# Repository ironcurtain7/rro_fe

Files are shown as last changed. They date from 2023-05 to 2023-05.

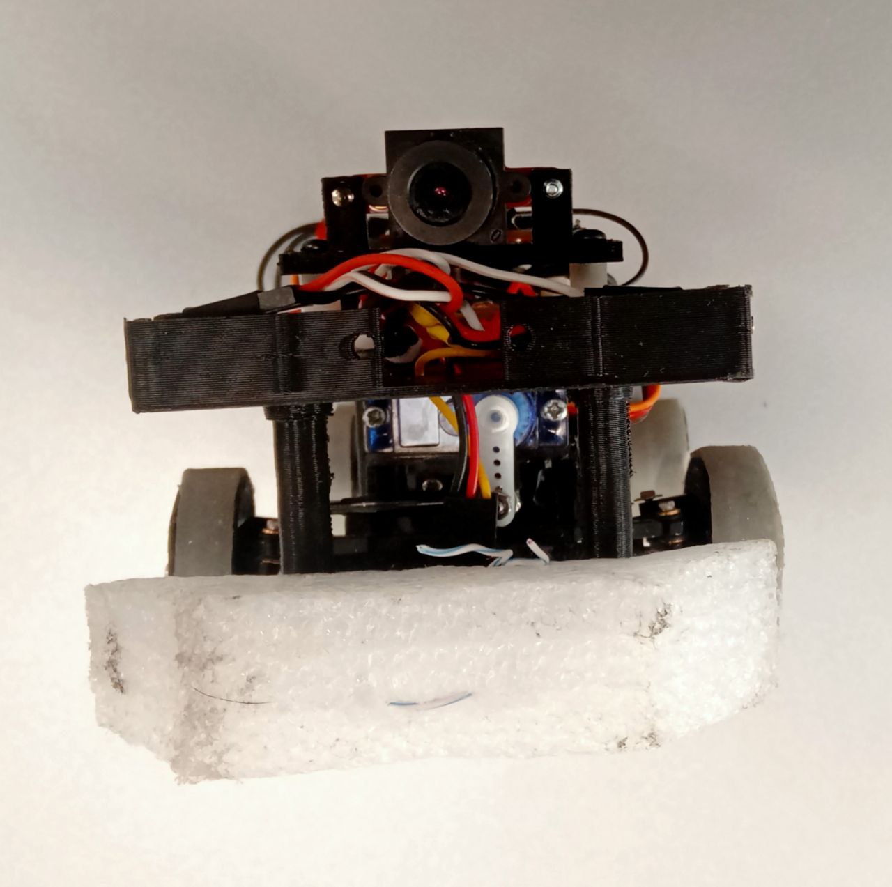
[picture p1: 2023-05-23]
v-photos/5.jpg

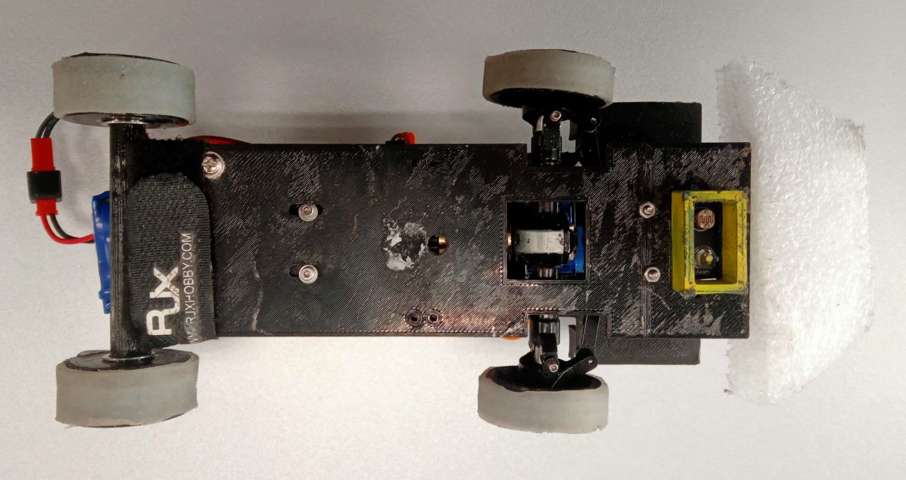
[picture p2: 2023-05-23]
v-photos/3.jpg

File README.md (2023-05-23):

Команда Роботикс (Robotx). Описание робота для соревновний FutureEngineers 2023.

Робот был сделан на основе самостоятельно разработанного и напечатанного на 3D-принтере шасси. 3D модели для печати находятся в папке models. 
Вариант самостоятельной разработки шасси был выбран по двум причинам: 
- возможность сделать шасси нужной конфигурации для оптимального расположения электронных и механических компонентов робота 
- уменьшения массы робота и улучшенния маневренности по сравнению с готовыми радиоуправляемыми шасси

Система перемещения робота:

Шасси робота состоит из следующих частей: 
непосредственно рамы шасси (car_frame.stl), 
креплений мотора, рулевого сервопривода и камеры (motor_mount.stl, servo_mount.stl,camera_mount.stl),
дисков колес (rim.stl) и вылитых из силикона шин (формы для отливки: wheels1.stl, wheels2.stl)

Шины решили делать из силикона, т.к. можно сделать любую необходимую форму шины и выбрать мягкость шины для максимального сцепления с поверхностью.

А так же используется передний мост от радиоуправляемой модели автомобиля размера 1/24 (Фото: other/axle.jpg) для того, чтобы сделать робота переднеприводным для улучшения маневренности. В мосту стоит 
червячный редуктор для уменьшения передаваемых на колеса оборотов от двигателя.

Основной двигатель: Readytosky rs2205, бесколлекторный, размера 2205, 2200 оборотов. Управляется через регулятор двигателя (модель LittleBee 30A-S) ШИМ-сигналом с ESP32. Возможен передний и задний ход.
Обороты двигателя выбраны исходя из передаточного числа редуктора в мосту 1 к 15.
Двигатель и привод переднего моста соединены латунной муфтой (Фото: other/muff.jpg).

Сервопривод поворота колес: Tower Pro MG90S, 9 грамм

Так как шасси было специально разработано для вышеуказанных компонентов, то все части шасси собираются вместе с помощью винтов и гаек M3/M4 без какой-либо дополнительной подготовки. 

Система питания:

В роботе используется одна батарея LiPo 2s (7.4V) 1100mAh. Подключена через выключатель. От нее через регулятор двигателя питается собственно двигатель. А так же через DC-DC 
преобразователь на 5В питается вся остальная электроника. Для сглаживания падения напряжения от работы двигателя в схеме предусмотрен конденсатор 16v, 2200мкФ, подключенный 
параллельно батарее.

Контроллеры и сенсоры:

В роботе используется два микроконтроллера: 
ESP32 - основной контроллер. Используется для выполнения всей логики программы, управления основным и рулевым приводом, обработка данных с датчиков.
OpenMV H7 - контроллер анализа изображения с камеры. Анализирует изображение, находит необходимые объекты и передает данные по найденным объектам в основной контроллер.
Передача происходит по Serial порту. Данные контроллеры были выбраны по причине малых размеров, низкого энергопотребления, большого количества портов для сенсоров
 и достаточной для данной задачи производительности.

Используемые сенсоры:

- лазерный дальномер VL53L0X - используется для определения расстояния до стен полигона. Установлены по одному справа и слева в передней части робота.
- фототранзистор со светодиодной подствекой - используется для определения цвета линий на поверхности полигона путем анализа яркости отражаемого света. Т.е. яркость отраженного света
от линий белого, синего и оранжевого цвета различается и на этой основе определяется цвет линий.
- кнопка старта робота

Схема подключения системы питания к контроллерам, двигателям, а так же сенсоров к контроллеру находится в папке schemes (scheme.jpg).
Для уменьшения количества проводов между контроллерами и датчиками была спроектирована в программе SprintLayot и вытравлена на текстолите плата, на которую уже паялись разъемы для контроллеров и подключались датчики.
Ее схема так же находится в папке schemes (Плата FE.lay6).

Робот включается с помощью выключателя на кабеле к батарее. Запускаются оба контроллера. После этого ESP32 инициализирует регулятор/основной двигатель (издается звуковой сигнал) и ждет нажатия на кнопку старта.

Логика работы программы:

Квалификационный заезд (робот устанавливается на поле строго вдоль бортов, основная программа начинает работать после нажатия кнопки старта):

1. Робот определяет свою позицию относительно стенок полигона. Т.е. определяет расстояние до стены справа и слева с помощью дальномеров.
2. Двигается вперед строго прямо до нахождения синей/оранжевой полосы с помощью датчика яркости света
3. Если найдена синяя/оранжевая полоса, то в зависимости от ранее определенной позиции, робот едет с поворотом колес налево/направо на нужный угол необходимое количество 
времени таким образом, чтобы подъехать к перпендикулярной стене на расстояние примерно 20см и встать вдоль нее. Угол и время проезда подбирается опытным путем.
4. Затем запускается блок программы езды вдоль внешней стены полигона с помощью дальномеров и PID-регулятора. Робот едет на расстоянии 20см от внешней стены. Т.е. если первый поворот был налево 
и внешняя стенка справа, то едем по правому дальномеру. И наоборот.
5. Во время езды вдоль стены анализируем показания датчика яркости и определяем наезд на синюю/оранжевую линию.
6. Если наехали на синюю/оранжевую линию, то робот поворачивает колеса на нужный угол налево/направо и проезжает неободимое количество времени для того, чтобы подъехать к 
перпендикулярной стене на расстояние 20см и встать вдоль нее. Угол и время проезда подбирается опытным путем.
7. Затем алгоритм повторяется с п.4 до тех пор пока количество поворотов не достигнет 12.
8. После проезда двенадцатого поворота проезжаем заранее подобранное время с заранее подобранным углом поворота колес и останавливаемся.

Финальный заезд (робот устанавливается на поле строго вдоль бортов, основная программа начинает работать после нажатия кнопки старта):
1. Робот определяет свою позицию относительно стенок полигона. Т.е. определяет расстояние до стены справа и слева с помощью дальномеров.
2. Двигается вперед строго прямо до нахождения синей/оранжевой полосы с помощью датчика яркости света.
3. Если найдена синяя/оранжевая полоса, то в зависимости от ранее определенной позиции, робот едет с поворотом колес налево/направо на нужный угол необходимое количество 
времени таким образом, чтобы подъехать к перпендикулярной стене на расстояние примерно 20см и встать вдоль нее. Угол и время проезда подбирается опытным путем.
4. Затем запускается блок программы езды вдоль внешней стены полигона с помощью дальномеров и PID-регулятора. Робот едет на расстоянии 20см от внешней стены. Т.е. если первый поворот был налево 
и внешняя стенка справа, то едем по правому дальномеру. И наоборот.
5. Во время езды вдоль стены анализируем показания с контроллера OpenMV H7. Если контроллер OpenMV находит препятствие, то передает данные о цвете и координатах препятствия на контроллер ESP32. 
ESP32 направляет робота в течение 1 секунды на препятсвие (постоянно получая данные с OpenMV о координатах препятсвия) для того, чтобы выровнять робота относительно препятствия. Т.е. препятсвие через одну секунду будет находиться строго перед роботом. 
Далее робот делает маневр объезда препятсвия в зависимости от цвета слева или справа. Объезд (углы поворота колес и время проезда) настраивается опытным путем. После объезда робот снова начинает ехать вдоль внешней стены.
6. Одновременно с получением данных с OpenMV, контроллер ESP32 анализирует показания датчика яркости и определяет наезд на синюю/оранжевую линию.
7. Если наехали на синюю/оранжевую линию, то робот поворачивает колеса на нужный угол налево/направо и проезжает неободимое количество времени для того, чтобы подъехать к 
перпендикулярной стене на расстояние 20см и встать вдоль нее. Угол и время проезда подбирается опытным путем.
8. Затем алгоритм повторяется с п.4 до тех пор пока количество поворотов не достигнет 12.
9. После проезда двенадцатого поворота проезжаем заранее подобранное время с заранее подобранным углом поворота колес и останавливаемся.

Программа для ESP32 написана на языке C++, для OpenMV - на языке python. Исходный код находится в папке src.

qual.cpp - программа для квалификационного заезда на ESP32

final.cpp - программа для финального заезда на ESP32

main.py - программа для контроллера OpenMV H7

Программы для ESP32 используют стандартные библиотеки из фреймворка PlatformIO, компилируются и загружаются в контроллер в среде Microsoft Visual Studio Code.
Программа для OpenMV H7 загружается в контроллер с помощью стандартной среды разработки от контроллеров OpenMV. (Скачать можно по ссылке https://openmv.io/pages/download)

Программы для квалификационного и финального заездов во многом схожи и состоят из таких блоков:
1. Блок добавления библиотек, определения переменных и создание объектов для управления сервоприводом, основным двигателем и дальномерами.
2. Функция SetID(). Инициализация лазерных дальномеров. Указание их режима и параметров работы.
3. Функция start(). Определение положения робота относительно стенок полигона, проезд до первого поворота, определение направления поворота и непосредственно выполнение поворота.
4. Функция setup(). Настройка параметров serial порта для передачи данных с контроллера OpenMV. Ожидание нажатия кнопки старта и запуск функции start() после нажатия кнопки.
5. Функция loop(). Основной цикл программы. В ней реализована вся логика программы описанная выше.

В программе для контроллера OpenMV H7 следующие блоки:
1. Импорт библиотек и определение переменных
2. Определение порогов цветов в цветовой модели LAB для определения объектов красного и зеленого цветов.
3. Настройка serial порта и режима работы камеры
4. Блок определения красных объектов в необходимой области видимости (ROI) и передача цвета и х-координаты в контроллер ESP32 по serial порту.
5. Блок определения зеленых объектов в необходимой области видимости (ROI) и передача цвета и х-координаты в контроллер ESP32 по serial порту.

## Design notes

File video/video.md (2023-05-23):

Квалификационный заезд: https://youtu.be/G_IELsaBGgg

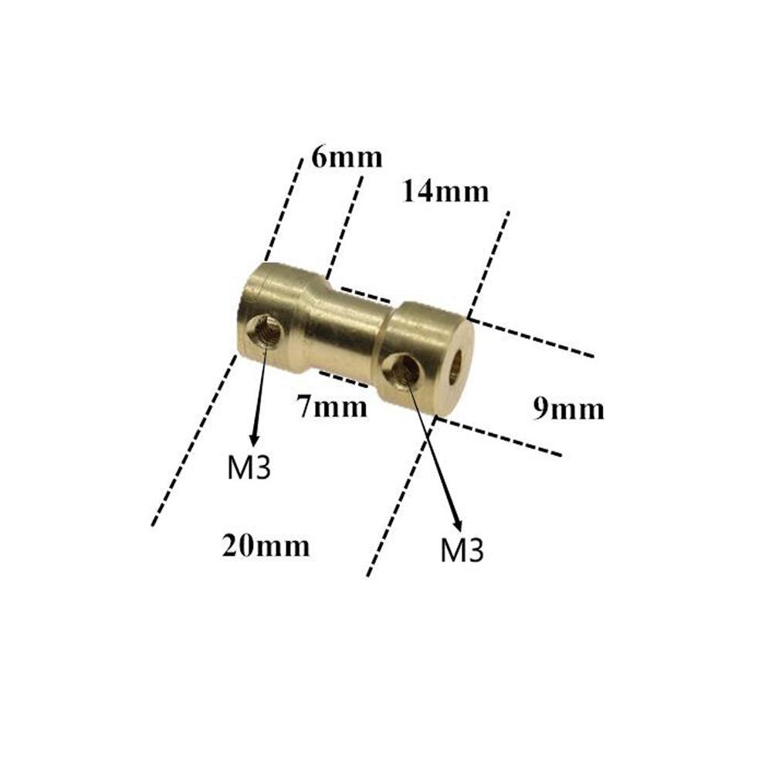
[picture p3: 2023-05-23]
other/muff.jpg

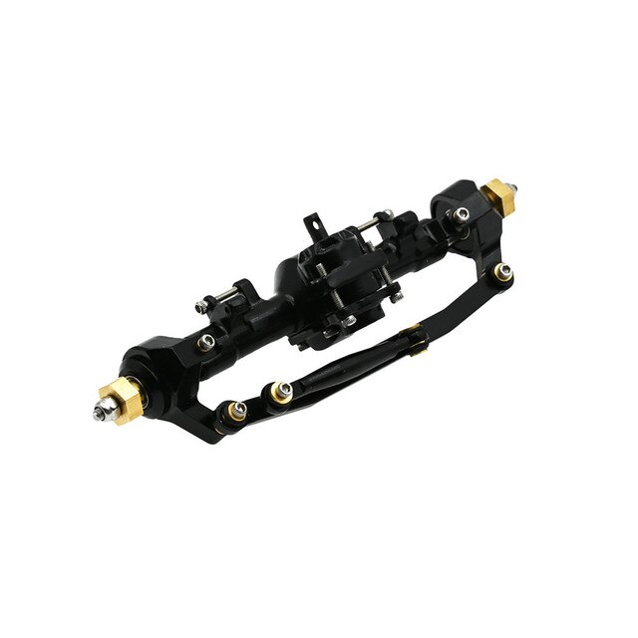
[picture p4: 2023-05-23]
other/axle.jpg

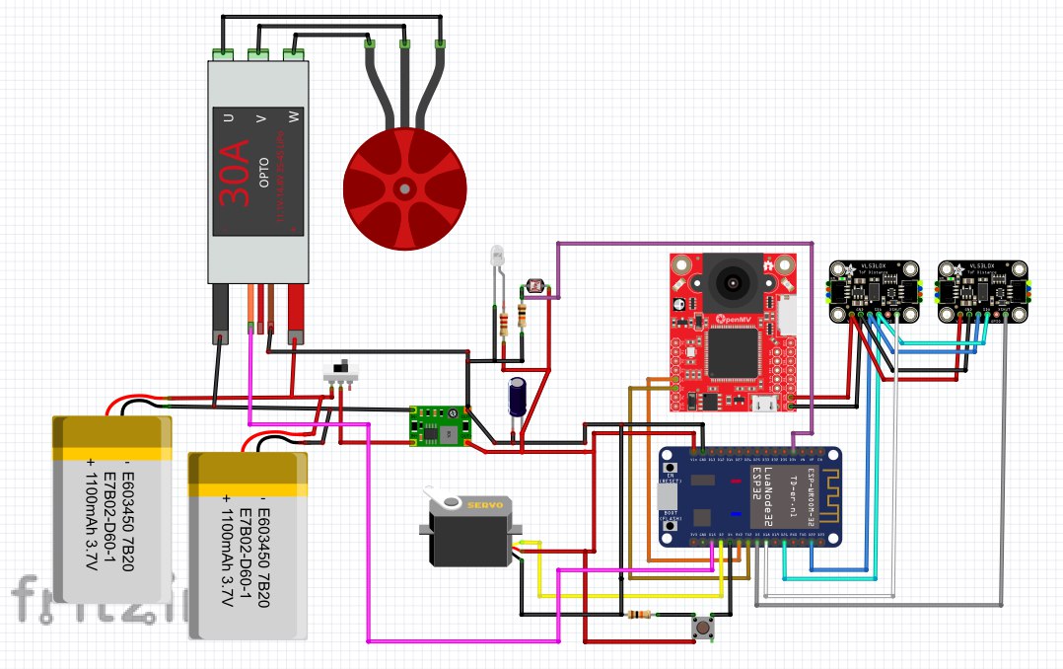
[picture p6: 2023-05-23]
schemes/scheme.jpg

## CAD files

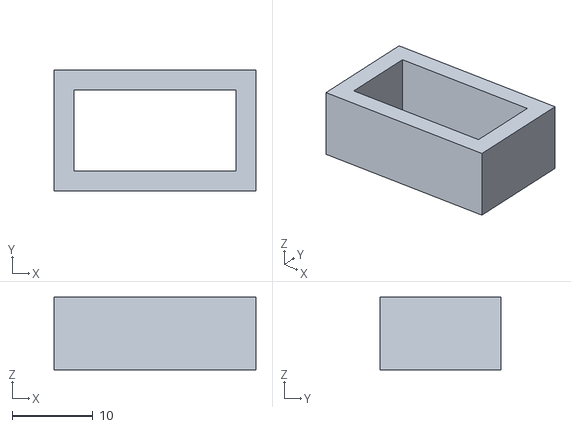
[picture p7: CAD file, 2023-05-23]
models/servo_mount.stl
25.0 x 15.0 x 9.00

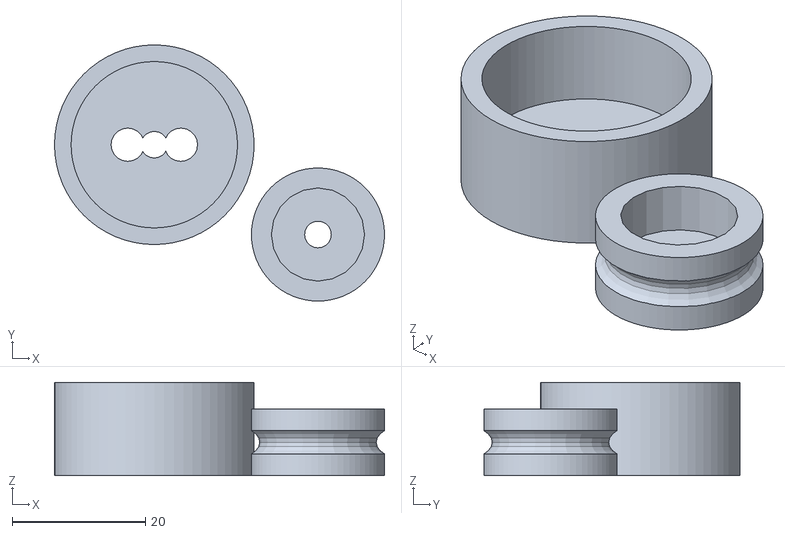
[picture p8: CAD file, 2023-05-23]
models/wheels2.stl
49.6 x 38.5 x 14.0

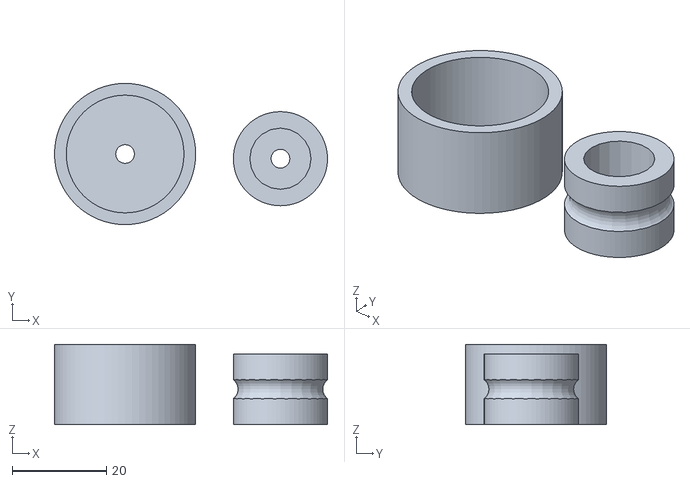
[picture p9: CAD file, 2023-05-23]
models/wheels1.stl
58.0 x 30.0 x 17.0

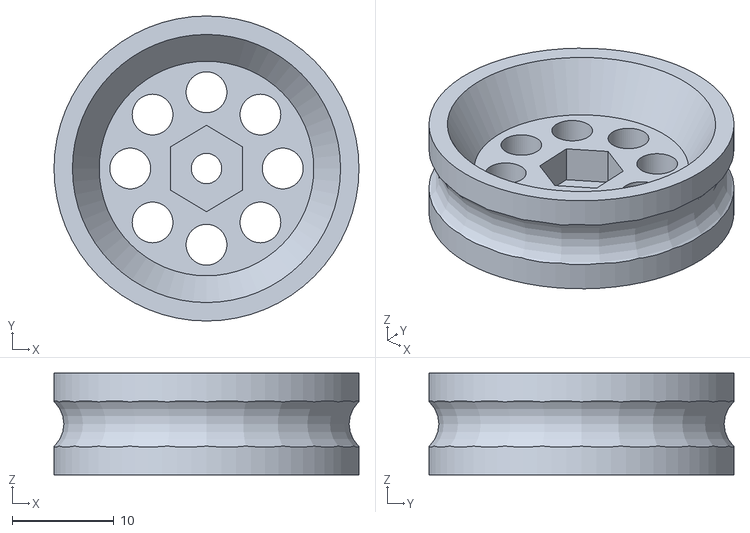
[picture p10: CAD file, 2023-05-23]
models/rim.stl
30.0 x 30.0 x 10.0

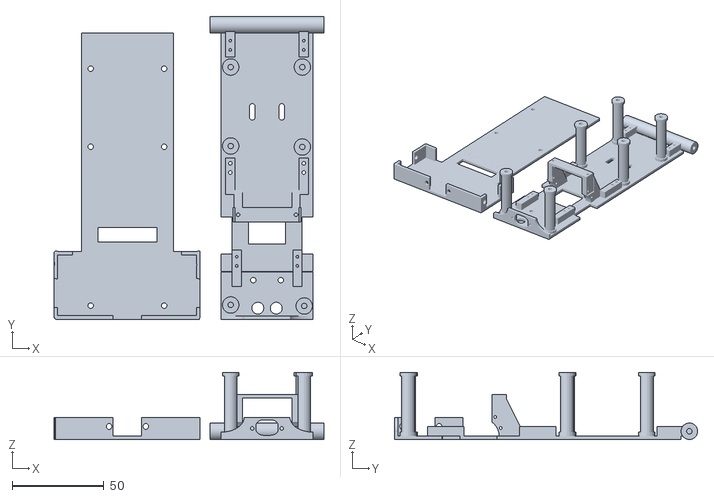
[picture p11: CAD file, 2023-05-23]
models/car_frame.stl
147.0 x 165.1 x 36.5

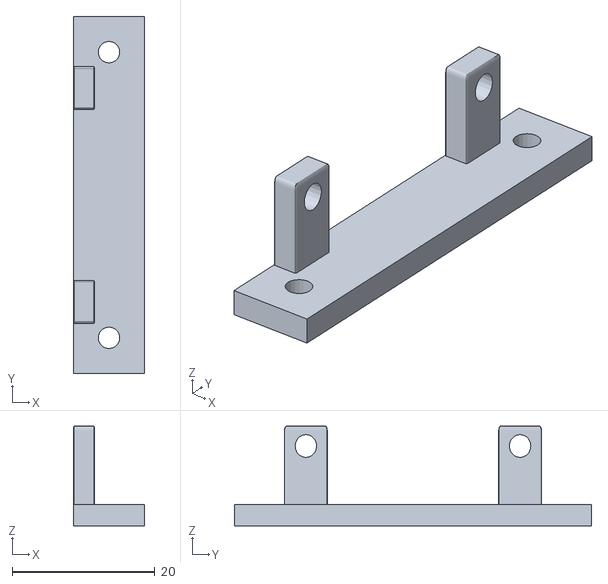
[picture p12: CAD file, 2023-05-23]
models/camera_mount.stl
10.0 x 50.0 x 14.0

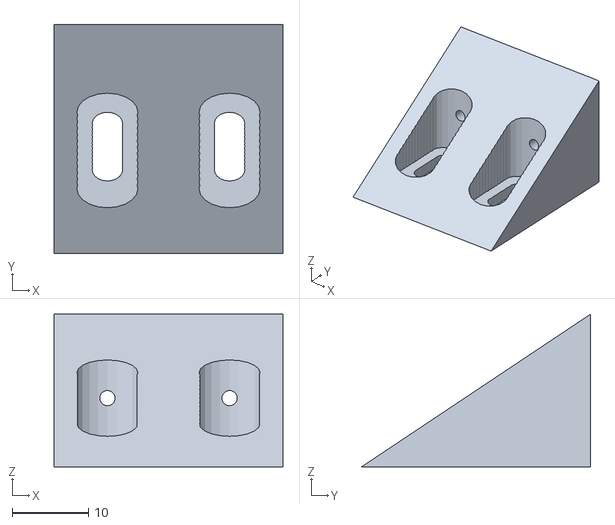
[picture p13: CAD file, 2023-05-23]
models/motor_mount.stl
30.0 x 30.0 x 20.0

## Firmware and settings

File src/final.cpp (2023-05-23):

// Добавление всех необходимых библиотек //
#include <Arduino.h>
#include "Adafruit_VL53L0X.h"
#include <Servo.h>

// Создание переменных //
#define RXD2 16
#define TXD2 17

int P;
int I;
int D;
int white = 3500;
int blue = 3270;
int timing = 700;
int lastError = 0, j, startflag, error;

int cx, millisold = 0;
int speed = 98;

int oldmil;
char color;
float Kp=0.1, Ki=0, Kd=1;
int16_t Fread, Lread, Rread, LigR, ButR = 0, count = 0;
const char* ssid = "DIR-615-effb";
const char* password = "18050523";
constexpr size_t size = 1000;
double numbers[size] {0}; 
int flag = 0, u, turn, porog;
int distance, sum  = 0, i = 0, sum1 = 0, Min = 9999;
int timMilis;
int timOLD;

int tim1 = 1000, tim2 = 1000, tim3 = 1000, ang1 = 65, ang2 = 65, ang3 = 65;







String Kp_text = String(Kp, 5);
String Ki_text = String(Ki, 5);
String Kd_text = String(Kd, 5);
String white_text = String(white);
String blue_text = String(blue);
String speed_text = String(speed);
String timing_text = String(timing);

String tim1_text = String(tim1);
String tim2_text = String(tim2);
String tim3_text = String(tim3);

String ang1_text = String(ang1);
String ang2_text = String(ang2);
String ang3_text = String(ang3);





// Adafruit_VL53L0X lox = Adafruit_VL53L0X();
Adafruit_VL53L0X lox1 = Adafruit_VL53L0X();
Adafruit_VL53L0X lox2 = Adafruit_VL53L0X();

Servo myservo;
Servo servo1;

void start(){  // Функция определения направления и положения ТС //

  servo1.write(84);

  while (i<10) {
    if (lox2.isRangeComplete()) {
    distance=lox2.readRange();
    if (distance < 999){
      Rread = distance;
      i=i+1;
      sum1 = sum1 + Rread;
    }
  }
  }

  Rread = sum1 / i;



if (Rread<550 && Rread>380){
turn=1;
Serial.print("Center1: ");
}
//Serial.println(Rread);


if (Rread>=550){
turn=2;
Serial.print("Left1: ");
}
//Serial.println(Rread);

if (Rread<=380){
  turn=3;
Serial.print("Right1: ");
}
//Serial.println(Rread);

myservo.write(103);
Serial.print("Turn: ");
Serial.println(turn);
Serial.print("dist: ");
Serial.println(Rread);






while (flag == 0){



LigR=analogRead(34);
//Serial.print(LigR);
//Serial.print("                        ");
sum=0;

if (LigR<white){
  for (i = 0; i < 10; i++) {
    LigR=analogRead(34);
    sum = sum + LigR;
  }

porog = sum/i;
Serial.println(porog);
if (porog<white){
flag = 1;
while (porog<white){


LigR=analogRead(34);
//Serial.print(LigR);
//Serial.print("                        ");
sum=0;

  for (i = 0; i < 10; i++) {
    LigR=analogRead(34);
    sum = sum + LigR;
  }

porog = sum/i;


  if (porog<Min){
    Min = porog;
  } 
}   
}
}
}





Serial.println(Min);

if (Min > blue){
  color = 'O';
Serial.print("ORANGE");

if (turn == 3){     // left
servo1.write(ang3);
delay(tim3);
servo1.write(84);
delay(200);

}
if (turn == 1){     // left
servo1.write(ang1);
delay(tim1);
servo1.write(84);
delay(200);

}
if (turn == 2){     // left
servo1.write(ang2);
delay(tim2);
servo1.write(84);
delay(200);

}

}
else{
  color = 'B';
Serial.print("BLUE");

if (turn == 2){     // left
servo1.write(104);
delay(1000);
servo1.write(84);
delay(200);
}
if (turn == 1){     // center
servo1.write(104);
delay(1000);
servo1.write(84);
delay(200);
}
if (turn == 3){     // right
servo1.write(104);
delay(1000);
servo1.write(84);
delay(200);

}

}




}

void RedTurn(){  // Функция объезда красного знака //
digitalWrite(13,1); // red
int redflag = 0;
int errold = 0;
int kp1 = 0.5;
int kd1 = 0;
cx = 60;
Serial.println("RED");
myservo.write(90);
delay(1000);
digitalWrite(13,0); // red

myservo.write(97);

int starttim = millis();
while (millis() - starttim < 1000){


  if (Serial2.available() > 0)
  { // если есть доступные данные

    String rd = Serial2.readStringUntil('\n');

    String rc = rd.substring(1,4);
    cx = rc.toInt();
    Serial.print(cx);
    
   
  }

  error = cx - 60;
  u = error * 0.5;// + kd1 * (error - errold);
  errold = error;

    if (u>30){
       u = 30;
    }
    if (u<-30){
       u = -30;
    }
   servo1.write(80-u);

}

myservo.write(100);
servo1.write(60);
delay(400);
servo1.write(105);
delay(450);

myservo.write(90);
//delay(5000);
millisold = millis();
}

void GreenTurn(){  // Функция объезда зеленого знака //
digitalWrite(12,1); // green

int redflag = 0;
int errold = 0;
int kp1 = 0.5;
int kd1 = 0;
cx = 60;
Serial.println("GREEN");
myservo.write(90);
delay(1000);
digitalWrite(12,0); // green

myservo.write(97);
int starttim = millis();
while (millis() - starttim < 1000){


  if (Serial2.available() > 0)
  { // если есть доступные данные

    String rd = Serial2.readStringUntil('\n');

    String rc = rd.substring(1,4);
    cx = rc.toInt();
    Serial.print(cx);
    
   
  }

  error = cx - 120;
 u = error * 0.5;// + kd1 * (error - errold);
  errold = error;

    if (u>30){
       u = 30;
    }
    if (u<-30){
       u = -30;
    }
   servo1.write(80-u);

}
myservo.write(100);
servo1.write(100);
delay(400);
servo1.write(55);
delay(450);

myservo.write(90);
//delay(5000);



millisold = millis();
}

void SetID() {  // Функция инициализации дальномеров //


digitalWrite(18,LOW);
digitalWrite(5,LOW);
delay(10);
digitalWrite(18,HIGH);
digitalWrite(5,HIGH);
delay(10);

digitalWrite(18,LOW);






digitalWrite(5,HIGH);

Serial.println("Adafruit VL53L0X test.");
  if (!lox1.begin(0x30)) {
    Serial.println(F("Failed to boot VL53L0X"));
   // while(1);
  }
  Serial.println(F("VL53L0X API Continuous Ranging example\n\n"));
  lox1.setMeasurementTimingBudgetMicroSeconds(20000);
  lox1.startRangeContinuous();




digitalWrite(18,HIGH);
Serial.println("Adafruit VL53L0X test.");
  if (!lox2.begin(0x32)) {
    Serial.println(F("Failed to boot VL53L0X"));
    //while(1);
  }
  Serial.println(F("VL53L0X API Continuous Ranging example\n\n"));
  lox2.setMeasurementTimingBudgetMicroSeconds(20000);
  lox2.startRangeContinuous();



}

void setup() {

pinMode(18,OUTPUT);
pinMode(5,OUTPUT);
pinMode(12,OUTPUT);
pinMode(13,OUTPUT);
pinMode(14,OUTPUT);


Serial.begin(115200);
Serial2.begin(115200, SERIAL_8N1, RXD2, TXD2);

  SetID();






  myservo.attach(15); 
  servo1.attach(2);
  servo1.write(84);
  myservo.write(90);
int iiiii = 0;

while (iiiii<7){
digitalWrite(13,1); // red
digitalWrite(12,0); // green
digitalWrite(14,0); // blue
delay(200);
digitalWrite(13,0); // red
digitalWrite(12,1); // green
digitalWrite(14,0); // blue
delay(200);
digitalWrite(13,0); // red
digitalWrite(12,0); // green
digitalWrite(14,1); // blue
delay(200);
digitalWrite(13,0); // red
digitalWrite(12,1); // green
digitalWrite(14,1); // blue
delay(200);
digitalWrite(13,0); // red
digitalWrite(12,0); // green
digitalWrite(14,0); // blue
delay(200);
iiiii = iiiii + 1;

}

  while (digitalRead(4) == 0){

  }

  //RedTurn();

digitalWrite(14,1); // blue
delay(500);
digitalWrite(14,0); // blue
 start();

}




void loop() {  // Основной цикл программы //


timMilis = millis();






int distance, sum, i = 0;

/*
  if (lox.isRangeComplete()) {
    Fread=lox.readRange();
    //Serial.print("FORWARD: ");
    //Serial.println(Fread);
  }
*/


if (color == 'B'){


  if (lox2.isRangeComplete()) {
    Rread = lox2.readRange();
    
    if (Rread > 1000){
      Rread = 1000;
    }
     error = 500 - Rread;

  }

      
}


else {


  if (lox1.isRangeComplete()) {
    Lread=lox1.readRange();

    if (Lread > 1000){
      Lread = 1000;
    }
      error = Lread - 500;

  }


}
      P = error;
      I = I + error;
      D = error - lastError;
      lastError = error;
      int u = P * Kp + D * Kd + I*Ki;
      //Serial.println(u);
      if (u>25){
        u = 25;
      }
      if (u<-25){
        u = -25;
      }
      myservo.write(speed);
      servo1.write(82 + u);


  LigR=analogRead(34);


if (color == 'B')
{


sum=0;
if (LigR<blue){
  for (i = 0; i < 10; i++) {
    LigR=analogRead(34);
    sum = sum + LigR;
  }

if (sum/i<white){
timOLD = millis();

servo1.write(109);

delay(1300);
servo1.write(82);
delay(200);

count = count + 1;
}
    
  }

}
else{


sum=0;
if (LigR>blue && LigR<white){
  for (i = 0; i < 5; i++) {
    LigR=analogRead(34);
    sum = sum + LigR;
  }

if (sum/i<white){
timOLD = millis();

servo1.write(59);

delay(1300);

servo1.write(82);
delay(200);



count = count + 1;
}
    
  }




}



if (count == 111){
//servo1.write(82);
////delay(500);
  //myservo.write(90);
//delay(10000000);
}




  if (Serial2.available() > 0)
  { // если есть доступные данные

    String rd = Serial2.readStringUntil('\n');

    String rc = rd.substring(1,4);
    cx = rc.toInt();
    Serial.print(cx);
    Serial.print("       ");
    Serial.println(rd);
    if (timMilis - millisold > 300 && cx<998){

    

    if (rd[0] == 'g'){
    //Serial.println("g");
    GreenTurn();
    }


    if (rd[0] == 'r'){
    //Serial.println("r");
    RedTurn();
    }


    }
   
  
  
  }  
   
  


  





}

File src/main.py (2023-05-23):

# Single Color RGB565 Blob Tracking Example
#
# This example shows off single color RGB565 tracking using the OpenMV Cam.

import sensor, image, time, math
from pyb import UART
threshold_index = 0 # 0 for red, 1 for green, 2 for blue

# Color Tracking Thresholds (L Min, L Max, A Min, A Max, B Min, B Max)
# The below thresholds track in general red/green/blue things. You may wish to tune them...
thresholds = [(0, 69, -118, -25, 7, 82)] # red
thresholds1 = [(21, 69, 27, 113, -13, 127)] # green
uart = UART(3, 115200)
sensor.reset()
sensor.set_pixformat(sensor.RGB565)
sensor.set_framesize(sensor.QQVGA)
sensor.skip_frames(time = 2000)
sensor.set_auto_gain(False) # must be turned off for color tracking
sensor.set_auto_whitebal(False) # must be turned off for color tracking
clock = time.clock()
blob=0
# Only blobs that with more pixels than "pixel_threshold" and more area than "area_threshold" are
# returned by "find_blobs" below. Change "pixels_threshold" and "area_threshold" if you change the
# camera resolution. "merge=True" merges all overlapping blobs in the image.
cx=0
flag=0
while(True):
    flag=0
    clock.tick()
    img = sensor.snapshot()
    for blob in img.find_blobs(thresholds, roi=(0, 65, 160, 76), pixels_threshold=100, area_threshold=100, merge=True):
        # These values depend on the blob not being circular - otherwise they will be shaky.
        if blob.elongation() > 0.5:
            img.draw_edges(blob.min_corners(), color=(255,0,0))
            img.draw_line(blob.major_axis_line(), color=(0,255,0))
            img.draw_line(blob.minor_axis_line(), color=(0,0,255))
            # These values are stable all the time.
        img.draw_rectangle(blob.rect())
        img.draw_cross(blob.cx(), blob.cy())
        # Note - the blob rotation is unique to 0-180 only.
        img.draw_keypoints([(blob.cx(), blob.cy(), int(math.degrees(blob.rotation())))], size=20)
        if blob.cx()>99:
            uart.write("g"+str(blob.cx())+"\n")
        if blob.cx()<100 and blob.cx()>9:
            uart.write("g0"+str(blob.cx())+"\n")
        if blob.cx()<10:
            uart.write("g00"+str(blob.cx())+"\n")


        print(blob.cx())

        flag=1




    for blob in img.find_blobs(thresholds1, roi=(0, 65, 160, 76), pixels_threshold=100, area_threshold=100, merge=True):
        # These values depend on the blob not being circular - otherwise they will be shaky.
        if blob.elongation() > 0.5:
            img.draw_edges(blob.min_corners(), color=(255,0,0))
            img.draw_line(blob.major_axis_line(), color=(0,255,0))
            img.draw_line(blob.minor_axis_line(), color=(0,0,255))
        # These values are stable all the time.
        img.draw_rectangle(blob.rect())
        img.draw_cross(blob.cx(), blob.cy())
        # Note - the blob rotation is unique to 0-180 only.
        #img.draw_keypoints([(blob.cx(), blob.cy(), int(math.degrees(blob.rotation())))], size=20)

        if blob.cx()>99:
            uart.write("r"+str(blob.cx())+"\n")
        if blob.cx()<100 and blob.cx()>9:
            uart.write("r0"+str(blob.cx())+"\n")
        if blob.cx()<10:
            uart.write("r00"+str(blob.cx())+"\n")
        print(blob.cx())

        flag=1




    if flag==0:
        uart.write("-1\n")
        print("999")


    #print(clock.fps())
